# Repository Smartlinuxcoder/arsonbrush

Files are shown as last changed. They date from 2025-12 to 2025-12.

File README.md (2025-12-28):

# Arsonbrush

Arsonbrush is a custom-made smart electric toothbrush, reusing a DC motor from a dead Oral-B toothbrush. 

## Why did I make this?

I was bored of $100+ dumb electric toothbrushes that have under-specced components to make them die faster.
For a bit of context, two well taken-care-of Oral-B toothbrushes stopped working, both with "exploded" resistors.
And also, ironically, whilst making this, ANOTHER ONE died on me.

I also noticed that there wasn't any open-source/DIY option.
So, may this toothbrush be the stepping stone for open-source electric toothbrushes in the future.

---
## Features!

- **Waterproof Charging**: Pogo pins!
- **Smart Base Station**: powered by ESP32C3
- **Huge Battery**: 5750mAh 21700 Li-Ion battery, do I need to say more?

(2+ years of runtime on a single charge, btw)

## Hardware Components

### Toothbrush Mainboard
- **MCU**: STM32C091FC
- **Motor Controller**: DRV8833RTYR dual H-bridge
- **IMU**: LSM6DSRTR 6-axis accelerometer/gyroscope
- **Charging IC**: MCP73831T-2ACI/OT (500mA charge rate)
- **Voltage Regulator**: MCP1700T-3302E/TT
- **Battery**: 21700 Li-Ion (5750mAh, BAK N21700CH-58E)
- **EMI Shield**: grounded 0.8mm copper sheet between motor and pcb

### Base Station
- **MCU**: Tenstar ESP32C3 SuperMini
- **Display**: Cheap I2C oled screen I have lying around
- **Connector**: 2A waterproof pogo pin connector pair
- **Status LED**: a status led

### 3D Model

3D Assembly

Case Front

Case Back

## Toothbrush PCB!
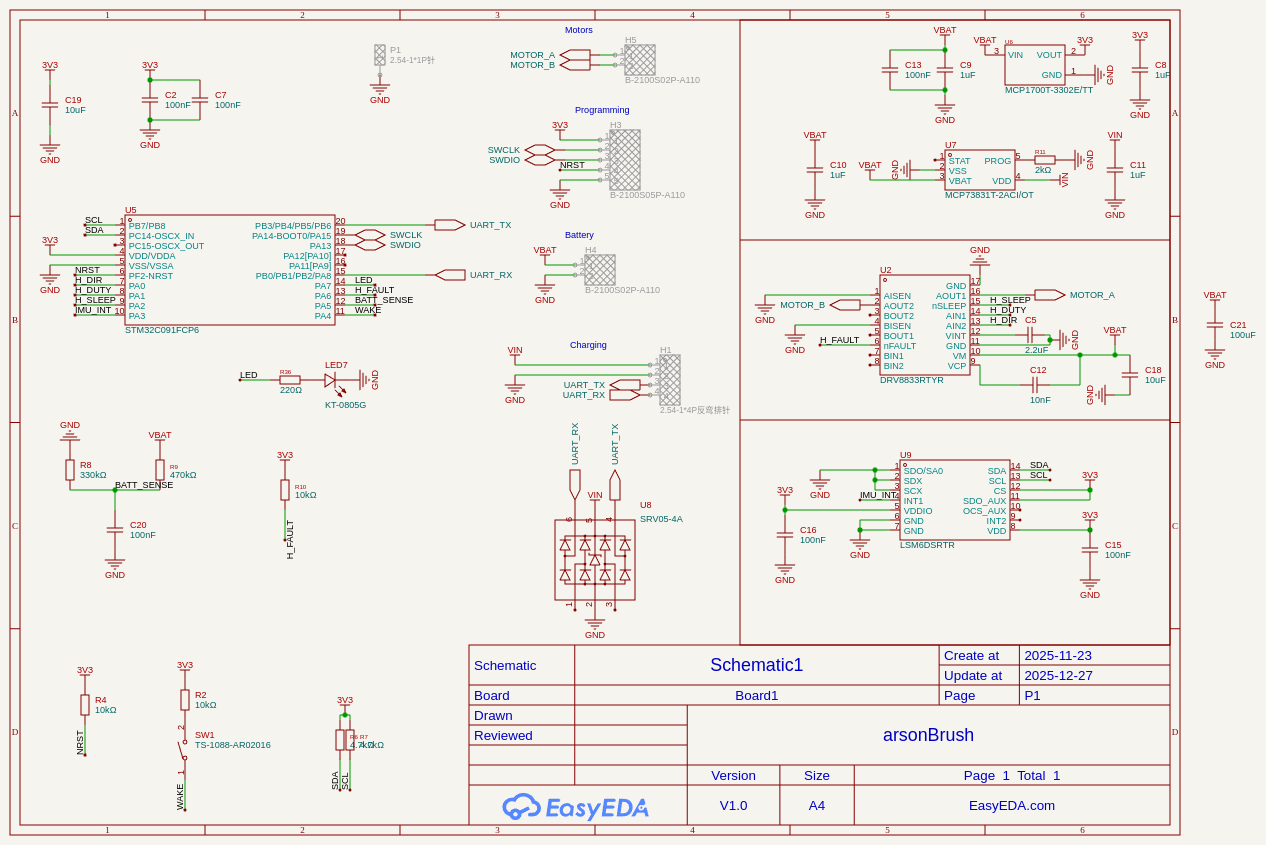
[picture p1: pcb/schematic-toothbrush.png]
Toothbrush Schematic

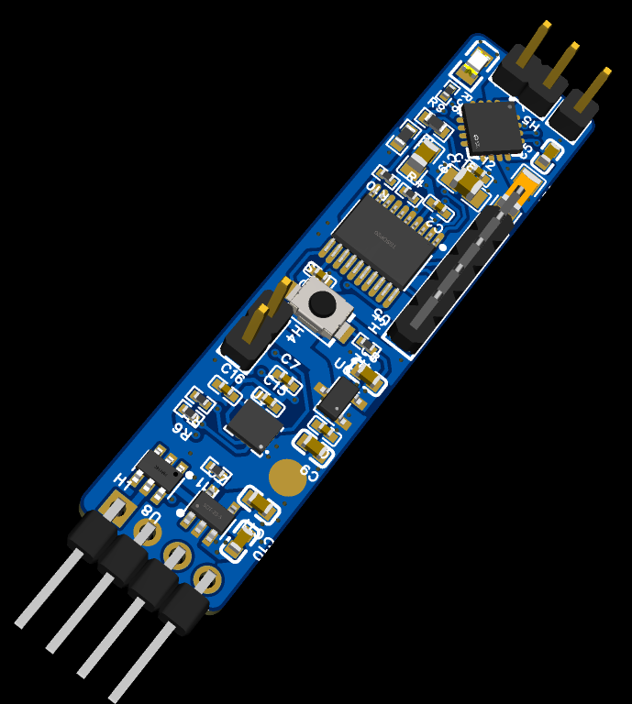
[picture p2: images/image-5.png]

## Base station PCB!
Base Station Schematic

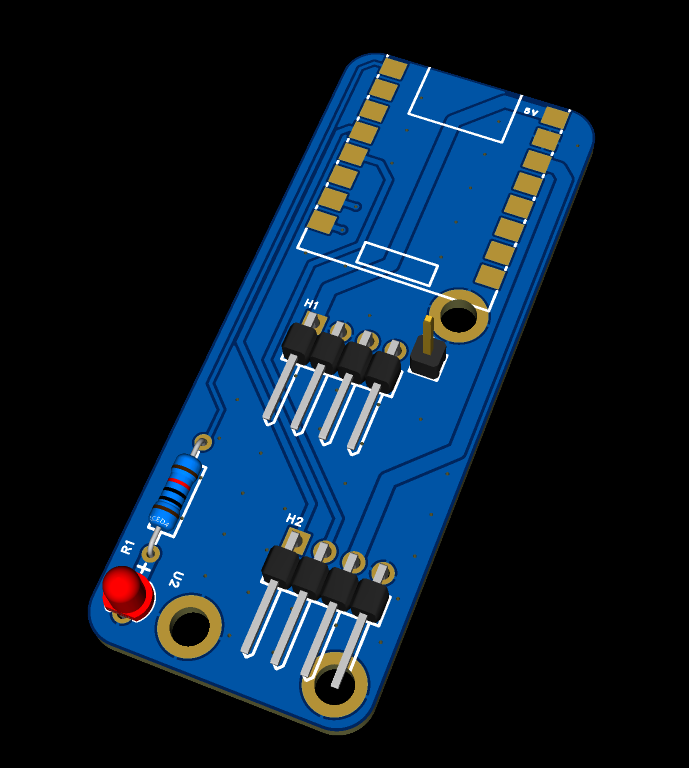
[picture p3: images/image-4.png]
Base Station PCB


## Bill of Materials
### This is in addition to [the toothbrush PCBA BOM](pcb/bom-toothbrush.csv)

| Component | Quantity | Description | Supplier | Unit Cost | Total Cost (+shipping) | Image |
|---|---|---|---|---|---|---|
| Toothbrush PCB | 5, 2 PCBA |toothbrush handle mainboard | JLCPCB | Not applicable | 60 EUR | |
| Base board | 5 | Toothbrush base PCB | JLCPCB | 1 EUR | 5 EUR | |
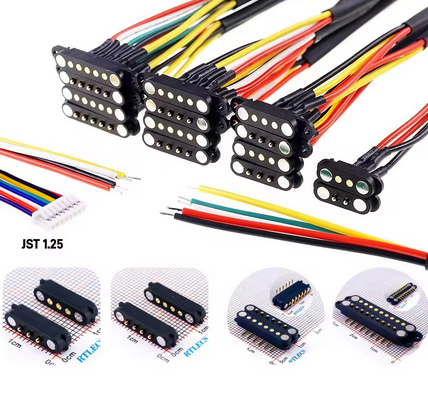
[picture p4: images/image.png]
| 2A Pogo pins connector pair | 1 pair | Waterproof connection | [Aliexpress](https://it.aliexpress.com/item/1005006525401310.html) | 5.89 EUR | 5.89 EUR | |
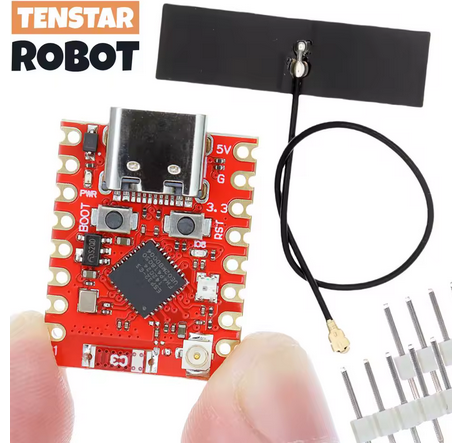
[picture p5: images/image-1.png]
| Tenstar ESP32C3 supermini | 1 | Base MCU | [Aliexpress](https://it.aliexpress.com/item/1005009897797706.html) | 3.36 EUR | 3.36 EUR | |
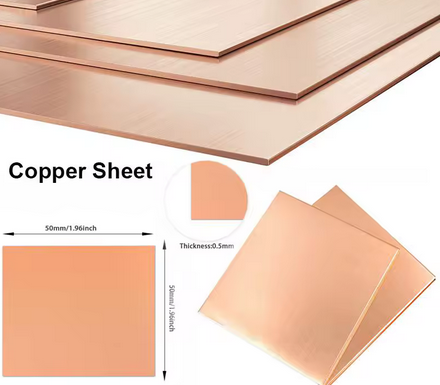
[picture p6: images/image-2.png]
| Copper sheet 0.8mm 50x50cm | 1 | Motor EMI protection plane | [Aliexpress](https://it.aliexpress.com/item/1005006915598911.html) | 3.69 EUR | 3.69 EUR | |
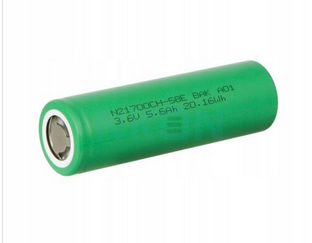
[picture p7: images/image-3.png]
| 21700 battery | 1 | Toothbrush battery | [nkon.nl](https://www.nkon.nl/en/bak-n21700ch-58e-5750mah-11-2a.html) | 3.75 EUR | 9.14 EUR | |

**Total Project Cost:** 90.56 EUR

**Notes:**
- All costs are in EUR
- Quantities reflect MOQ

## File tree
```
arsonbrush/
├── 3d/                    # 3D models and case designs
├── code/arsonbrush/       # Firmware
│   ├── Core/Src           # Firmware source code
├── pcb/                   # EasyEDA PCB
│   ├── arsonBrush.eprj    # Complete project
│   ├── bom-toothbrush.csv # toothbrush PCBA BOM
│   ├── gerber-base.zip    # Base station gerbers
│   ├── gerber-toothbrush.zip # Toothbrush gerbers
│   ├── schematic-base.pdf # Base station schematic
│   └── schematic-toothbrush.pdf # Toothbrush schematic
├── datasheets/            # Component datasheets
└── README.md              # This file!
```

## Building the Toothbrush firmware

### Prerequisites
- Nix pakage manager
- ST-Link or compatible programmer

### Compilation
```bash
cd code/arsonbrush
nix-shell
make
```

### Flashing
Flash the generated `.bin/.hex` from `/build`

## License

This project is licensed under the [GNU General Public License v3.0](LICENSE).

## Acknowledgments

- Project developed as part of Hack Club Blueprint
- Awesome thanks to DragonSlayer and Adam Turaj for helping me make this!

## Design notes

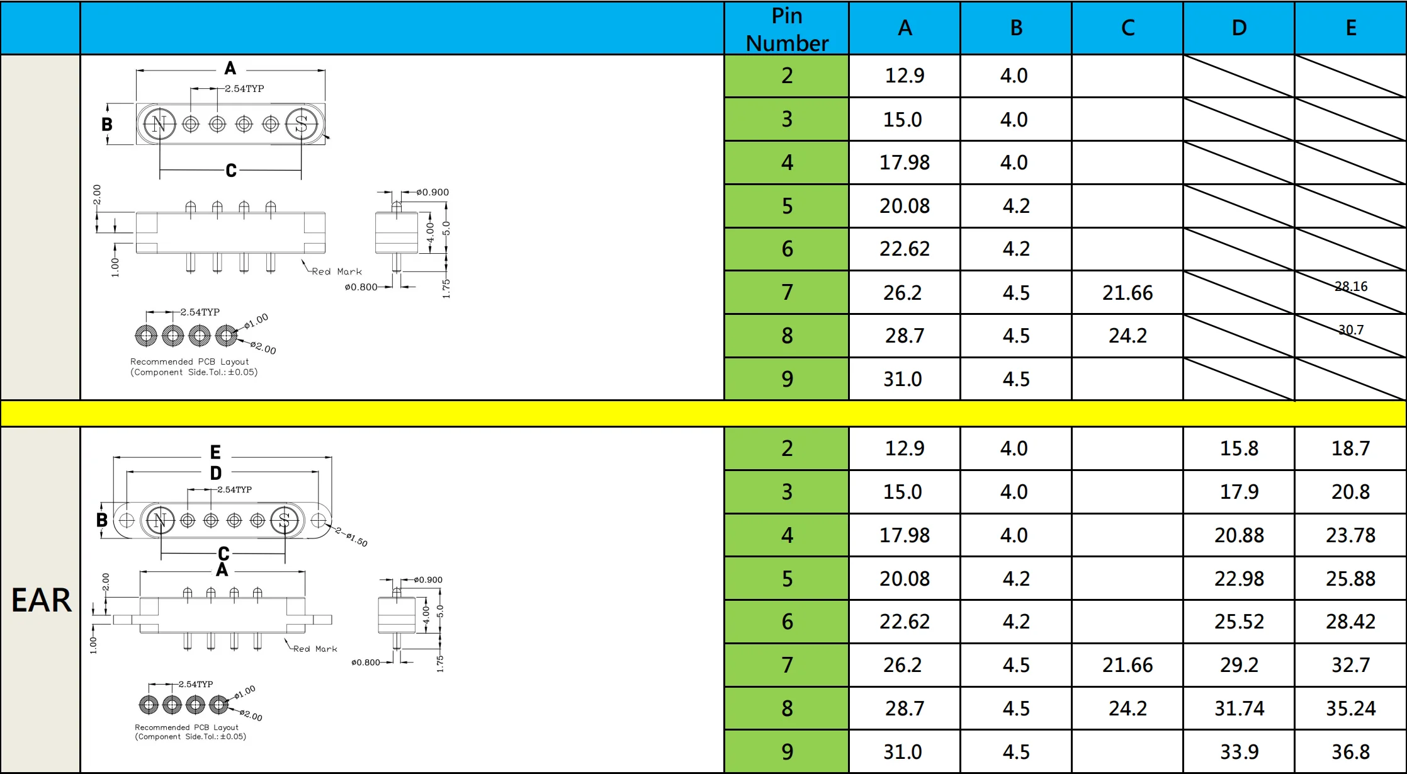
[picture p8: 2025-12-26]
datasheets/pogo.webp

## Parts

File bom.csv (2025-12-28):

Component | Quantity | Description | Supplier | Unit Cost | Total Cost (+shipping) | Link
Toothbrush PCB !!SEE bom-toothbrush.csv!! | 5 (2 PCBA) | toothbrush handle mainboard | JLCPCB | Not applicable | 60 EUR
Base board | 5 | Toothbrush base PCB | JLCPCB | 1 EUR | 5 EUR
2A Pogo pins connector pair | 1 pair | Waterproof connection | Aliexpress | 5.89 EUR | 5.89 EUR | https://it.aliexpress.com/item/1005006525401310.html
Tenstar ESP32C3 supermini | 1 | Base MCU | Aliexpress | 3.36 EUR | 3.36 EUR | https://it.aliexpress.com/item/1005009897797706.html
Copper sheet 0.8mm 50x50cm | 1 | Motor EMI protection plane | Aliexpress | 3.69 EUR | 3.69 EUR | https://it.aliexpress.com/item/1005006915598911.html
21700 battery | 1 | Toothbrush battery | nkon.nl | 3.75 EUR | 9.14 EUR | https://www.nkon.nl/en/bak-n21700ch-58e-5750mah-11-2a.html

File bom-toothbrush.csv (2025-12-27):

No. | Quantity | Comment | Designator | Footprint | Value | Manufacturer Part | Manufacturer | Supplier Part | Supplier | LCSC Price | Name
1 | 6 | 100nF | C2,C7,C13,C15,C16,C20 | C0402 | 100nF | CL05B104KO5NNNC | SAMSUNG(三星) | C1525 | LCSC |  | 100nF
2 | 1 | 2.2uF | C5 | C0603 | 2.2uF | CL10A225KO8NNNC | SAMSUNG(三星) | C23630 | LCSC |  | 2.2uF
3 | 4 | 1uF | C8,C9,C10,C11 | C0603 | 1uF | CL10A105KB8NNNC | SAMSUNG(三星) | C15849 | LCSC |  | 1uF
4 | 1 | 10nF | C12 | C0402 | 10nF | CL05B103KB5NNNC | SAMSUNG(三星) | C15195 | LCSC |  | 10nF
5 | 2 | 10uF | C18,C19 | C0805 | 10uF | CL21A106KAYNNNE | SAMSUNG(三星) | C15850 | LCSC |  | 10uF
6 | 1 | 100uF | C21 | C1206 | 100uF | CL31A107MQHNNNE | SAMSUNG(三星) | C15008 | LCSC |  | 100uF
7 | 1 | KT-0805G | LED7 | LED0805-R-RD |  | KT-0805G | KENTO | C2297 | LCSC |  | KT-0805G
8 | 2 | 10kΩ | R2,R4 | R0402 | 10kΩ | 0402WGF1002TCE | UNI-ROYAL(厚声) | C25744 | LCSC |  | 10kΩ
9 | 2 | 4.7kΩ | R6,R7 | R0402 | 4.7kΩ | 0402WGF4701TCE | UNI-ROYAL(厚声) | C25900 | LCSC |  | 4.7kΩ
10 | 1 | 330kΩ | R8 | R0603 | 330kΩ | 0603WAF3303T5E | UNI-ROYAL(厚声) | C23137 | LCSC |  | 330kΩ
11 | 1 | 470kΩ | R9 | R0603 | 470kΩ | 0603WAF4703T5E | UNI-ROYAL(厚声) | C23178 | LCSC |  | 470kΩ
12 | 1 | 10kΩ | R10 | R0402 | 10kΩ | 0402WGJ0103TCE | UNI-ROYAL(厚声) | C25531 | LCSC |  | 10kΩ
13 | 1 | 2kΩ | R11 | R0402 | 2kΩ | 0402WGF2001TCE | UNI-ROYAL(厚声) | C4109 | LCSC |  | 2kΩ
14 | 1 | 220Ω | R36 | R0402 | 220Ω | 0402WGF2200TCE | UNI-ROYAL(厚声) | C25091 | LCSC |  | 220Ω
15 | 1 | TS-1088-AR02016 | SW1 | SW-SMD_L3.9-W3.0-P4.45 |  | TS-1088-AR02016 | XUNPU(讯普) | C720477 | LCSC |  | TS-1088-AR02016
16 | 1 | DRV8833RTYR | U2 | QFN-16_L4.0-W4.0-P0.65-TL-EP2.6 |  | DRV8833RTYR | TI(德州仪器) | C154936 | LCSC |  | DRV8833RTYR
17 | 1 | STM32C091FCP6 | U5 | TSSOP-20_L6.5-W4.4-P0.65-LS6.4-BL |  | STM32C091FCP6 |  | C45338507 | LCSC |  | STM32C091FCP6
18 | 1 | MCP1700T-3302E/TT | U6 | SOT-23-3_L2.9-W1.6-P1.90-LS2.8-BR |  | MCP1700T-3302E/TT | MICROCHIP(美国微芯) | C39051 | LCSC |  | MCP1700T-3302E/TT
19 | 1 | MCP73831T-2ACI/OT | U7 | SOT-23-5_L3.0-W1.7-P0.95-LS2.8-BL |  | MCP73831T-2ACI/OT | MICROCHIP(美国微芯) | C424093 | LCSC |  | MCP73831T-2ACI/OT
20 | 1 | SRV05-4A | U8 | SOT-23-6_L2.9-W1.6-P0.95-LS2.9-BL |  | SRV05-4A | R+O(宏嘉诚) | C20615829 | LCSC |  | SRV05-4A
21 | 1 | LSM6DSRTR | U9 | LGA-14_L3.0-W2.5-P0.50-BR |  | LSM6DSRTR | ST(意法半导体) | C784817 | LCSC |  | LSM6DSRTR

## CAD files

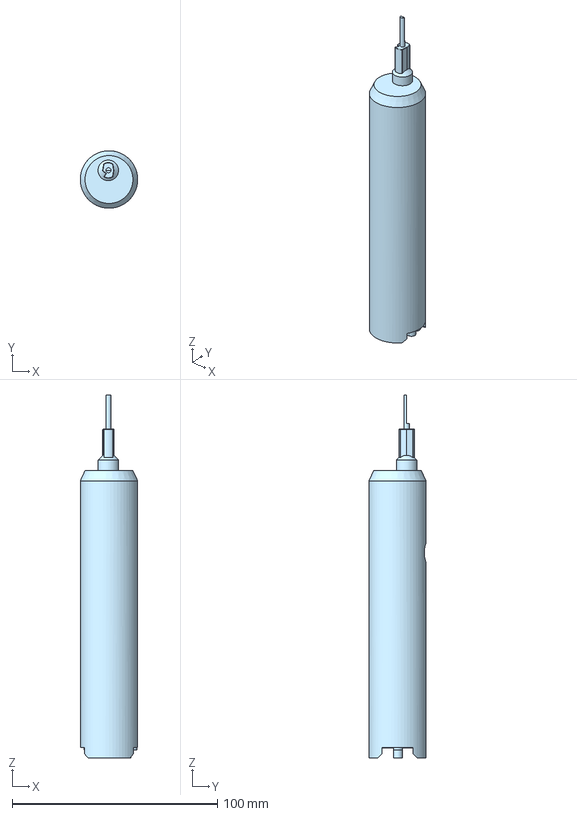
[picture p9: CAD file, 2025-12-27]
3d/Assembly.step
28.0 x 28.0 x 176.9 mm
W4bN-Board
OralB_Bracket

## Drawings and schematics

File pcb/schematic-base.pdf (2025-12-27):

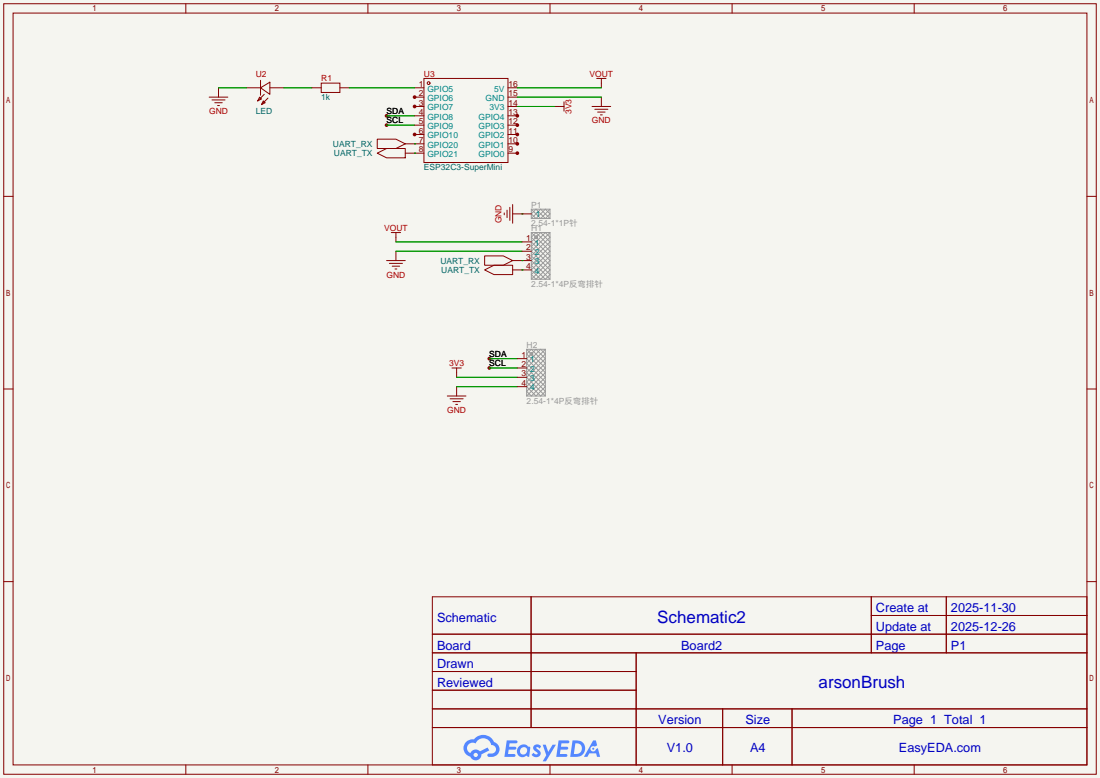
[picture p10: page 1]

Schematic | Schematic2 | Create at | 2025-11-30

Update at | 2025-12-26

Board | Board2 | Page | P1
Drawn | | arsonBrush
Reviewed

Version | Size | Page 1 Total 1
V1.0 | A4 | EasyEDA.com

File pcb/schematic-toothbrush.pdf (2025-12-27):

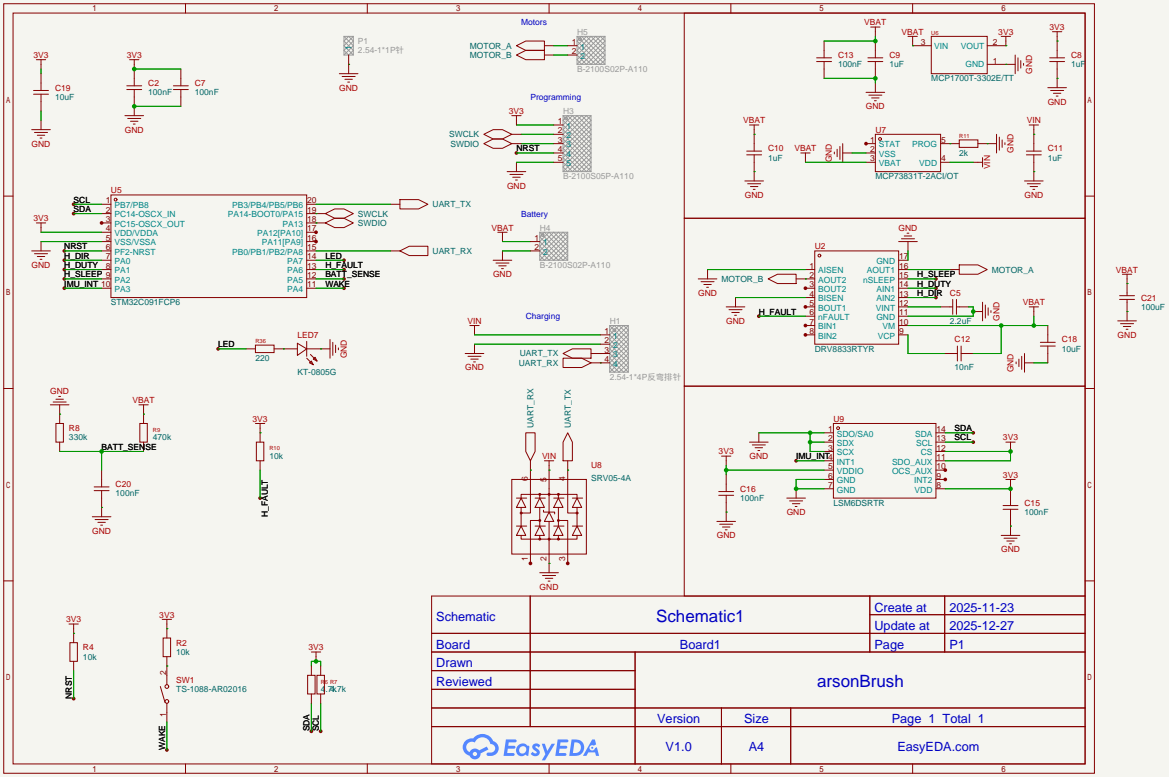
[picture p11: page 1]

VM 10 GND 11 VINT 12 AIN2 13 AIN1 14 nSLEEP 15 AOUT1 16 GND 17

Schematic | Schematic1 | Create at | 2025-11-23

Update at | 2025-12-27

Board | Board1 | Page | P1
Drawn | | arsonBrush
Reviewed

Version | Size | Page 1 Total 1
V1.0 | A4 | EasyEDA.com

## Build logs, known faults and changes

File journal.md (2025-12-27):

<!--
  This journal is auto generated by Hack Club Blueprint.
-->

## 11/28/2025 - Looking for components  

_Time spent: 4.5h_  

Heyo!
I wanna try making an electric toothbrush, I am reusing a perfectly fine dc motor I harvested from a dead Oral-b toothbrush.
I want to make both the toothbrush pcb and a base for it
Settled on the MSPM0C1104 microcontroller, DRV8833RTYR motor controller, MPU-6050 for the IMU, and the CN3058E for charging.
You might notice that I'm not using any regulator for my components, this is beacuse I am using a LiFePO4 battery (voltage goes up to 3v6).
The base station will most probably house an esp32 and will connect to the brush via audio jack.
The cases will be designed in 3D and printed on my own printer I have at home.



## 12/21/2025 - Schematic done!  

_Time spent: 6.5h_  


I made the schematic, switched out the MSPM0 for an STM32C0.
took a long time figuring out datasheets and pins to wire.
I have set the charging speed via a resistor to 300mA. that means that charging a 18650 will take ~10 hours.
I have added the brush button to a WAKE pin of the stm32 so I can make it go to sleep when not in use.
I have also made a rough sketch on Onshape for the sizes, it'll be roughly 16cm long and hopefully I will manage to house the pcb vertically, sandwiched between battery and case.


## 12/23/2025 - Routedmaxxed  

_Time spent: 10.0h_  


Finished the schematic, added battery sensor functionality,and a bit more decoupling for the motors.
Fixed IMU caps to follow the datasheet.
Routed entire board, (with multiple iterations)




Made it all fit in 1.2cm of width! (same as an oral-b toothbrush, though I have A LOT more components)

## 12/26/2025 11 AM - Newer IMU!  

_Time spent: 1.0h_  

I went to check the final price of the PCB, and it was over 80$ and I saw that a lot of money went to the MPU6050.
I looked at the other option and settled on the far better LSM6DSRTR, which reduced the total cost to a more sensible 60$.




On a sidenote, I also managed to find some nice Pogo pin connectors and a nice battery to add, but that's for another journal  

## 12/26/2025 10 PM - 3D model + base PCB!  

_Time spent: 5.0h_  

I added a grounded copper sheet sandwitched between the motor and the pcb, to reduce EMI and providing a nice, big, low impedance ground.
[I also chose the pogo pins to use, the base MCU, and the perfect battery.](https://github.com/Smartlinuxcoder/arsonbrush)
put all in a 3D model:


Added a case:
Screenshot From 2025-12-26 21-59-03
Screenshot From 2025-12-26 21-58-58

And this is done!

Now time for the base pcb:
I added the supermini, an oled screen I have lying around and a resistor+led for status

And routed it!


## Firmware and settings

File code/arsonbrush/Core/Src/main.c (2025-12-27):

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
/* Includes ------------------------------------------------------------------*/
#include "main.h"

/* USER CODE BEGIN Includes */
#include <string.h>
/* USER CODE END Includes */

ADC_HandleTypeDef hadc1;

I2C_HandleTypeDef hi2c1;

TIM_HandleTypeDef htim2;

UART_HandleTypeDef huart1;

/* USER CODE BEGIN PV */
volatile uint8_t button_pressed = 0;
uint8_t system_state = 0; // 0: OFF, 1: ON
uint8_t rx_byte;
uint8_t rx_index = 0;
/* USER CODE END PV */

void SystemClock_Config(void);
static void MX_GPIO_Init(void);
static void MX_ADC1_Init(void);
static void MX_FLASH_Init(void);
static void MX_I2C1_Init(void);
static void MX_TIM2_Init(void);
static void MX_USART1_UART_Init(void);
/* USER CODE BEGIN 0 */
void HAL_GPIO_EXTI_Callback(uint16_t GPIO_Pin)
{
  if (GPIO_Pin == GPIO_PIN_4)
  {
    button_pressed = 1;
  }
}

void HAL_UART_RxCpltCallback(UART_HandleTypeDef *huart)
{
  if (huart->Instance == USART1)
  {
    if (rx_index == 0)
    {
      if (rx_byte == 'H')
      {
        rx_index = 1;
      }
    }
    else if (rx_index == 1)
    {
      if (rx_byte == 'i')
      {
        uint8_t msg[] = "Hello";
        HAL_UART_Transmit(&huart1, msg, 5, 100);
        rx_index = 0;
      }
      else if (rx_byte == 'H')
      {
        rx_index = 1;
      }
      else
      {
        rx_index = 0;
      }
    }
    HAL_UART_Receive_IT(&huart1, &rx_byte, 1);
  }
}
/* USER CODE END 0 */

/**
  * @brief  The application entry point.
  * @retval int
  */
int main(void)
{

  /* MCU Configuration--------------------------------------------------------*/

  /* Reset of all peripherals, Initializes the Flash interface and the Systick. */
  HAL_Init();

  /* Configure the system clock */
  SystemClock_Config();

  /* Initialize all configured peripherals */
  MX_GPIO_Init();
  MX_ADC1_Init();
  MX_FLASH_Init();
  MX_I2C1_Init();
  MX_TIM2_Init();
  MX_USART1_UART_Init();
  /* USER CODE BEGIN 2 */
  HAL_NVIC_SetPriority(USART1_IRQn, 1, 0);
  HAL_NVIC_EnableIRQ(USART1_IRQn);
  HAL_UART_Receive_IT(&huart1, &rx_byte, 1);
  
  // Calibrate ADC
  HAL_ADCEx_Calibration_Start(&hadc1);
  /* USER CODE END 2 */

  /* Infinite loop */
  /* USER CODE BEGIN WHILE */
  while (1)
  {
    if (button_pressed)
    {
      button_pressed = 0;
      
      if (system_state == 1)
      {
        // Go eep
        HAL_GPIO_WritePin(GPIOA, GPIO_PIN_7, GPIO_PIN_RESET);
        HAL_TIM_PWM_Stop(&htim2, TIM_CHANNEL_2);
        HAL_GPIO_WritePin(GPIOA, GPIO_PIN_0, GPIO_PIN_RESET);
        system_state = 0;
      }
      else
      {
        // slow adc read
        HAL_Delay(32);
        
        HAL_ADC_Start(&hadc1);
        if (HAL_ADC_PollForConversion(&hadc1, 100) == HAL_OK)
        {
          uint32_t adc_val = HAL_ADC_GetValue(&hadc1);
          HAL_ADC_Stop(&hadc1);
          
          // voltage divider: 470k + 330k = 800k total
          // V_adc = V_bat * 330k / 800k
          // V_bat = adc_val * 3.3V * 800k / (4095 * 330k)
          // V_bat = adc_val * 3300mV * 800 / (4095 * 330)
          uint32_t battery_mv = (adc_val * 3300 * 800) / (4095 * 330);
          
          if (battery_mv > 3400)
          {
            HAL_GPIO_WritePin(GPIOA, GPIO_PIN_7, GPIO_PIN_SET);
            
            // PWM 50% duty cycle 12MHz / 500 = 24kHz
            __HAL_TIM_SET_COMPARE(&htim2, TIM_CHANNEL_2, 250);
            HAL_TIM_PWM_Start(&htim2, TIM_CHANNEL_2);
            
            HAL_GPIO_WritePin(GPIOA, GPIO_PIN_0, GPIO_PIN_SET); // PA0
            system_state = 1;
          }
          else
          {
            for (int i = 0; i < 2; i++)
            {
              HAL_GPIO_WritePin(GPIOA, GPIO_PIN_7, GPIO_PIN_SET);
              HAL_Delay(500);
              HAL_GPIO_WritePin(GPIOA, GPIO_PIN_7, GPIO_PIN_RESET);
              HAL_Delay(500);
            }
            system_state = 0;
          }
        }
      }
    }
    
    if (system_state == 0)
    {
      HAL_SuspendTick();
      HAL_PWR_EnterSLEEPMode(PWR_MAINREGULATOR_ON, PWR_SLEEPENTRY_WFI);
      HAL_ResumeTick();
    }
    /* USER CODE END WHILE */

    /* USER CODE BEGIN 3 */
  }
  /* USER CODE END 3 */
}

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


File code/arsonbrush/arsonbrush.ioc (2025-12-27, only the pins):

Mcu.UserName=STM32C091FCPx
PA0.Signal=GPIO_Output
PA1.Signal=S_TIM2_CH2
PA13.Signal=DEBUG_SWDIO
PA14-BOOT0.Signal=DEBUG_SWCLK
PA2.Signal=GPIO_Output
PA3.Signal=GPIO_Input
PA4.Signal=GPXTI4
PA5.Signal=ADC1_IN5
PA6.Signal=GPIO_Input
PA7.Signal=GPIO_Output
PA8.Signal=USART1_RX
PB6.Signal=USART1_TX
PB7.Signal=I2C1_SCL
PC14-OSCX_IN(PC14).Signal=I2C1_SDA

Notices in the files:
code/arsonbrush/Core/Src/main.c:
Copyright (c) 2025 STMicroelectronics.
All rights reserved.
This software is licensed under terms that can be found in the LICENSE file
